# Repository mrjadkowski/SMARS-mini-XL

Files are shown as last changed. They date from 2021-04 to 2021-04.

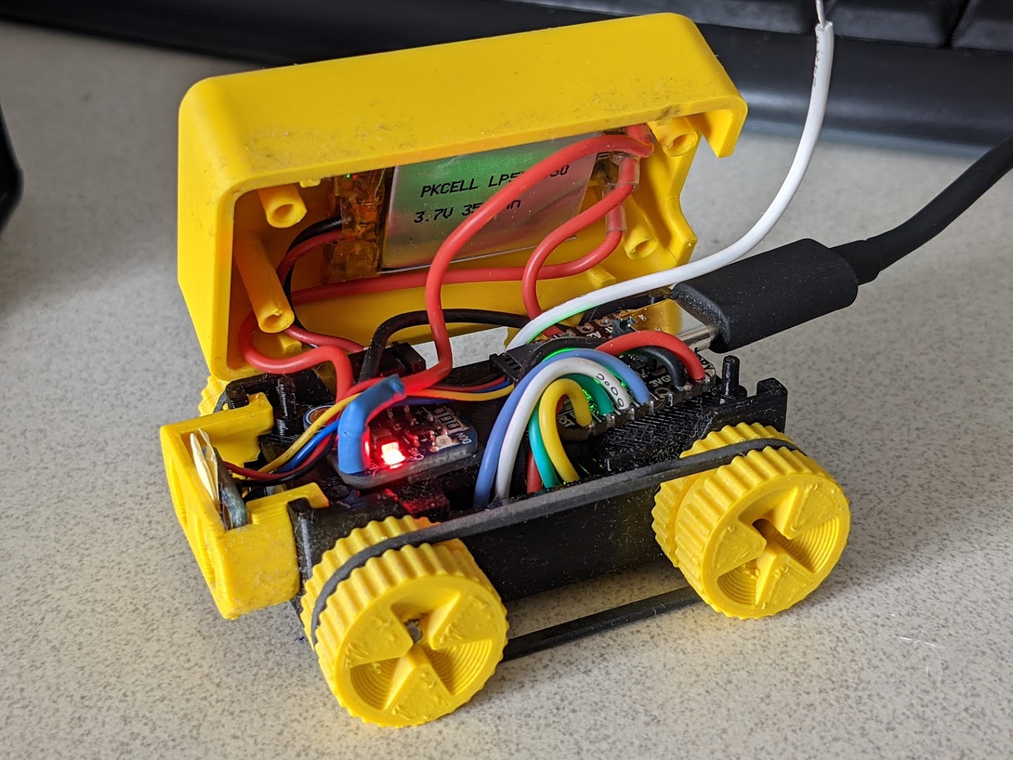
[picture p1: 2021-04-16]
Media/1.x.x/1.0.0 wiring.jpg

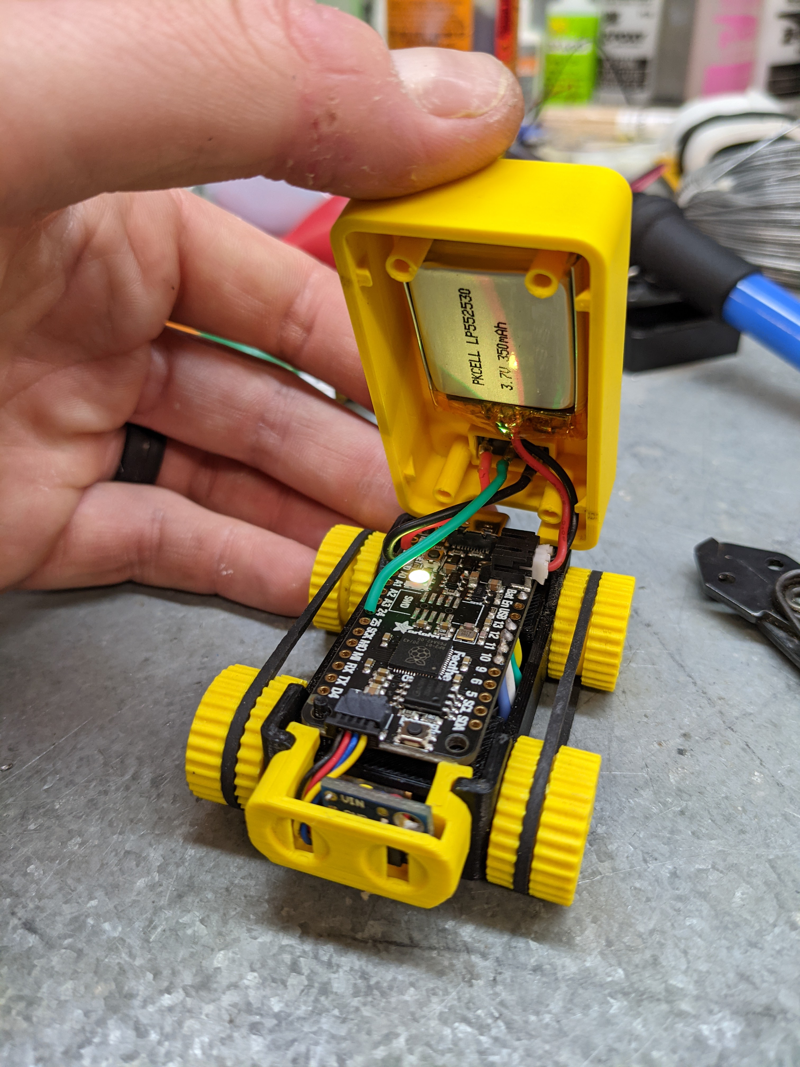
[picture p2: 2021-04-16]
Media/2.x.x/2.0.0 wiring.jpg

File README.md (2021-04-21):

# SMARS-mini-XL
### A small wheeled or tracked robot running on Circuit Python

Stemma QT board carrier face

#### I noticed that there has been a bump in traffic the last few days. I would love to have some collaborators on this project. I'm brand new to programming, brand new to CAD, brand new to GitHub, and brand new to 3D printing. About the only exiting skill I bring to this is soldering. Post an issue if you have a suggestion for a change, revise the 3D model, fork the code and improve it if you want, go crazy! I honestly have no idea what I'm doing and I know it can all be done better.

This repository has the 3D models, wiring details, and code for the SMARS mini XL. Currently the code is designed for Circuit Python 6.2.0 running on an Adafruit Feather RP2040. It uses a VL53L0X time-of-flight sensor and an APDS-9960 proximity/gesture/color/light sensor connected with i2c, an DRV8833 h-bridge motor driver, a small lipo, and a SPST switch. The code currently includes basic light seeking behavior while driving forward, obstacle detection and avoidance, and stuck detection that triggers an "unstuck" maneuver.

This project started as a remix of the "SMARS mini" design by [Kevin McAleer](https://www.youtube.com/user/kevinmcaleer28). I don't think it shares a single part with that design anymore, but it was an excellent starting point and gave the project an aesthetic theme that has certainly carried on. Thanks Kevin!

.STL and .STEP files are available in the CAD files folder (probably the most current) and at: https://www.thingiverse.com/thing:4810626

Current hardware BOM (this is the list of parts you need to buy and links to buy them): https://docs.google.com/spreadsheets/d/167UUY43PvzWUNg7vgtmYUr31faELwSrEWL3U5X_r1nM/edit?usp=sharing

The Media folder has a bunch of pictures and videos of various versions of the robot, including pictures of the wiring to see how things are routed.

Current code is running on the 2.x.x hardware setup. For the QT Py version, see the 1.1.0 release

See the Fritzing diagram for wiring.

See the code for the current required libraries; at the moment it requires:

  - adafruit_bus_device
  - adafruit_vl53l0x
  - adafruit_neopixel
  - adafruit_motor
  - adafruit_debouncer
  - adafruit_apds9960

The following parameters can be changed in the setup section of the code to alter the behavior:

  - start_turn_distance: the distance from an obstacle that the robot will stop and begin to pivot right
  - turn_time: the amount of time the robot will pivot to the right once started
  - stop_turn_distance: the distance from an obstacle that the robot will stop pivoting and start driving forward again, assuming turn_time has elapsed
  - abort_turn_time: if the robot has not reached stop_turn_distance in this amount of time while pivoting, it will attempt an unstuck maneuver
  - stuck_variance: if the robot moves less than this distance in 1 second, a stuck_counter event is recorded.

The NeoPixel on the RP2040 is used to show different states. The color codes are:
  - Green: driving forward
  - Red: obstacle detected and turning
  - Blue: stuck event detected, performing unstuck maneuver
  - Bright white: three consecutive unstuck maneuvers have failed

### Upcoming planned releases:
  - 3.0.0: Addition of solar charging, light-seeking behavior, and sleep logic to the 2.0.0 driving behavior. The end goal is to allow the robot to run perpetually, always trying to keep the battery charged as much as possible.

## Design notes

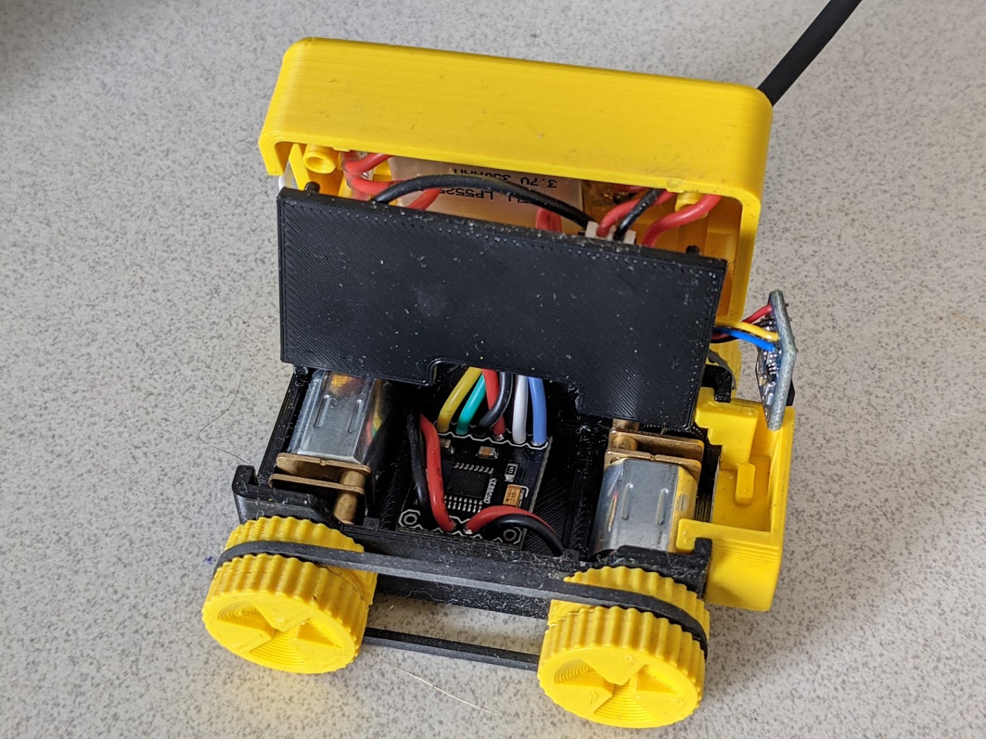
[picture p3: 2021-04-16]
Media/1.x.x/motors and driver.jpg

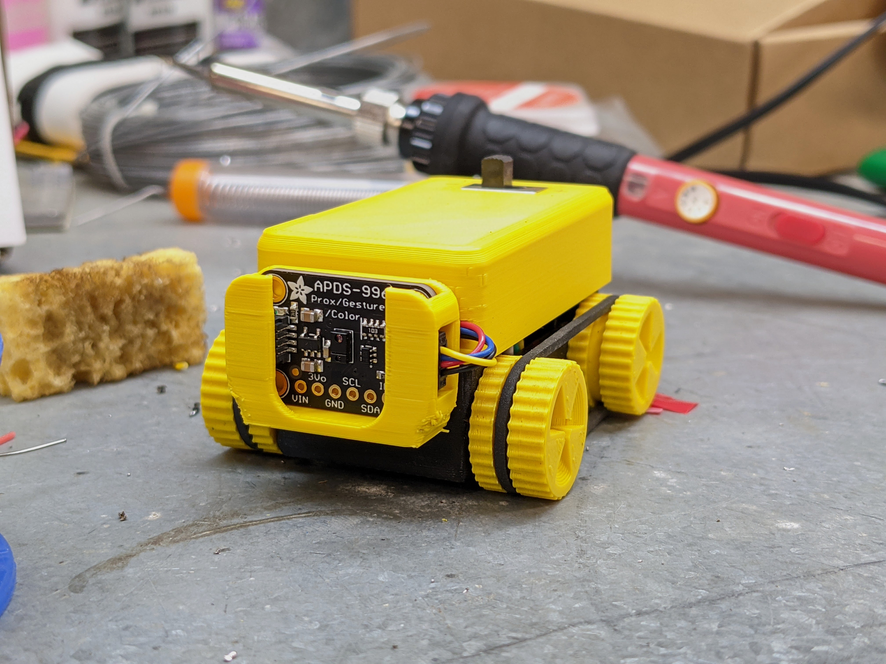
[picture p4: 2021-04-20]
Media/2.x.x/Stemma QT board carrier face.jpg

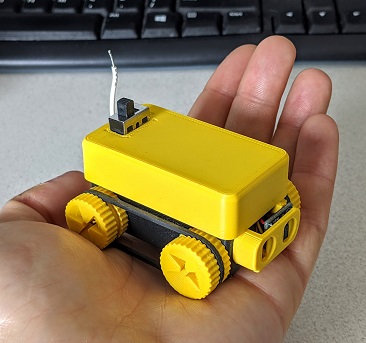
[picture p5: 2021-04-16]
Media/1.x.x/handheld.jpg

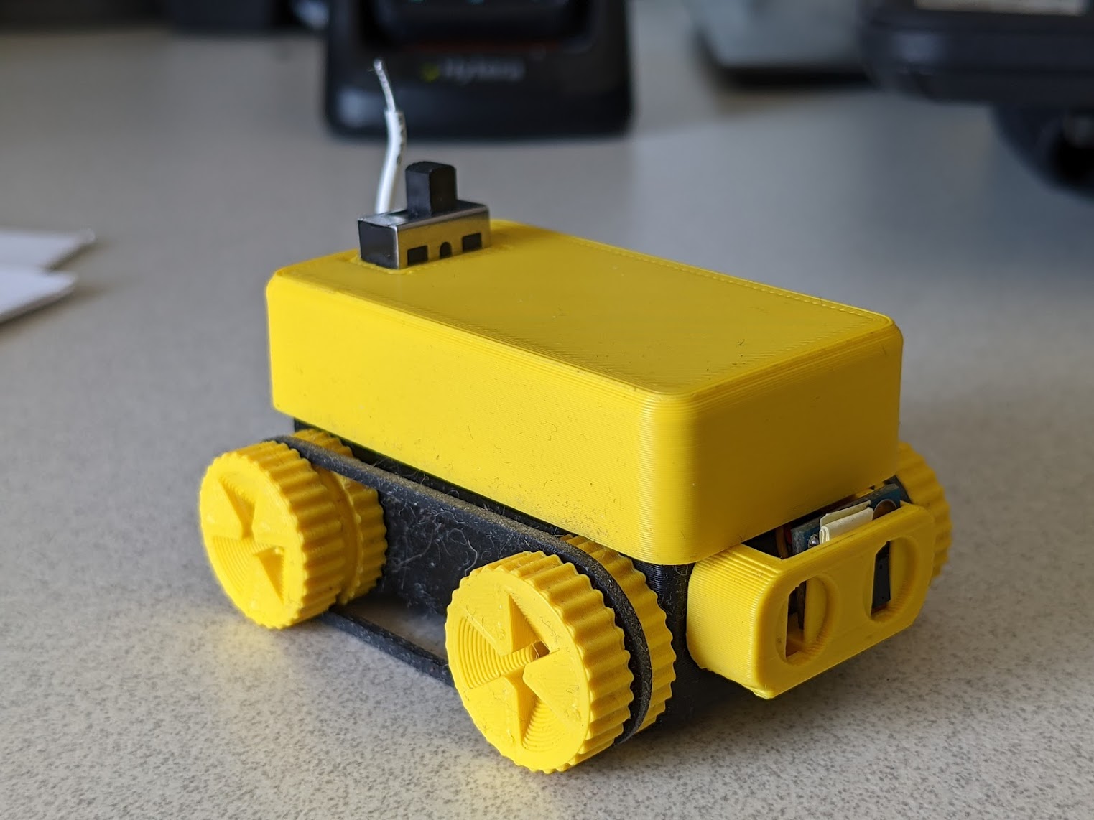
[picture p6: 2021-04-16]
Media/1.x.x/1.0.0.jpg

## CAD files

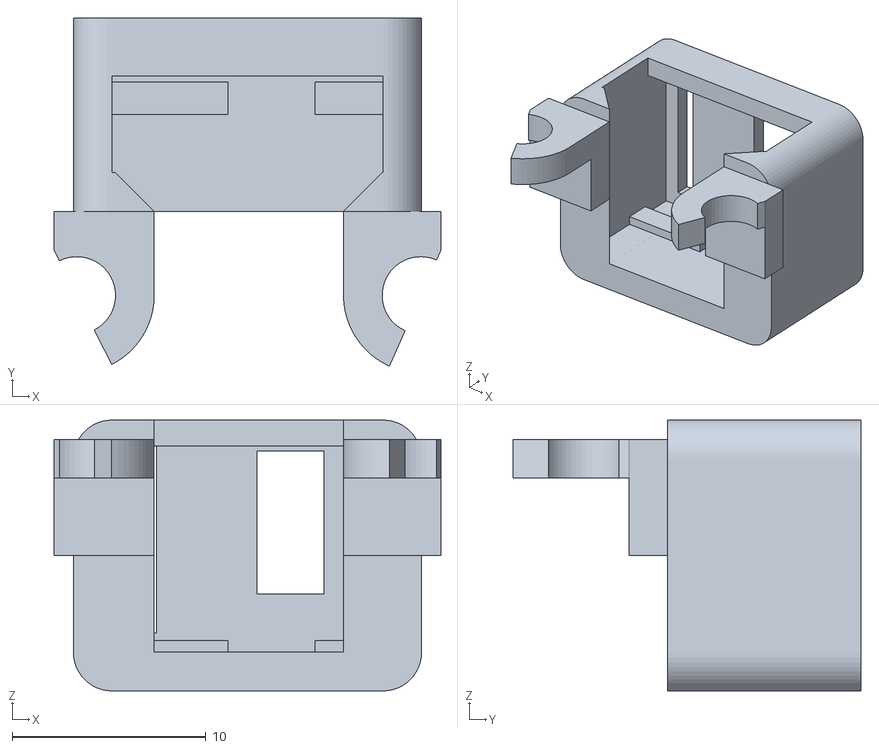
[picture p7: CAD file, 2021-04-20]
CAD files (STL and STEP)/GY-530 Rear Carrier.stl
20.0 x 18.0 x 14.0

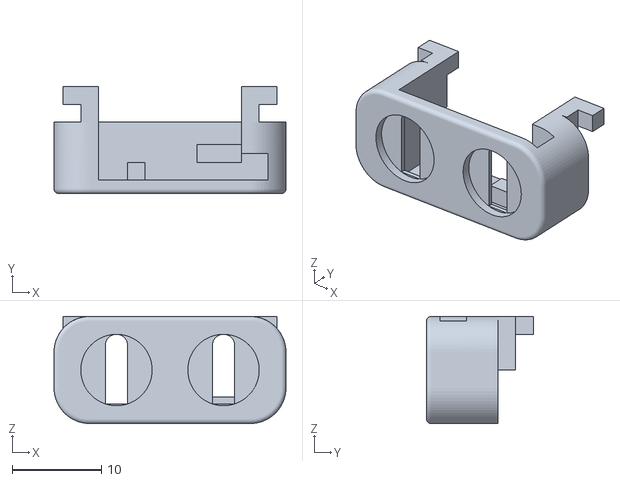
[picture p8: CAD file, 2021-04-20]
CAD files (STL and STEP)/GY-530 Face.stl
26.0 x 12.0 x 12.0

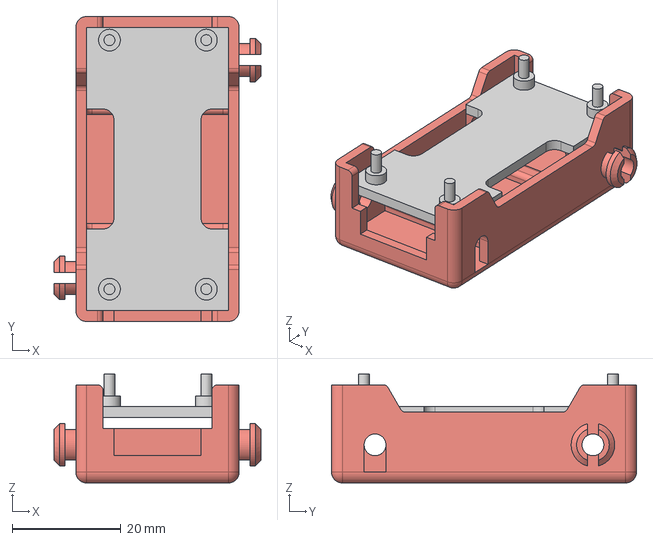
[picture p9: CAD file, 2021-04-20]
CAD files (STL and STEP)/SMARS mini XL 2-0-0.step
38.0 x 56.0 x 20.0 mm
Chassis
Feather support

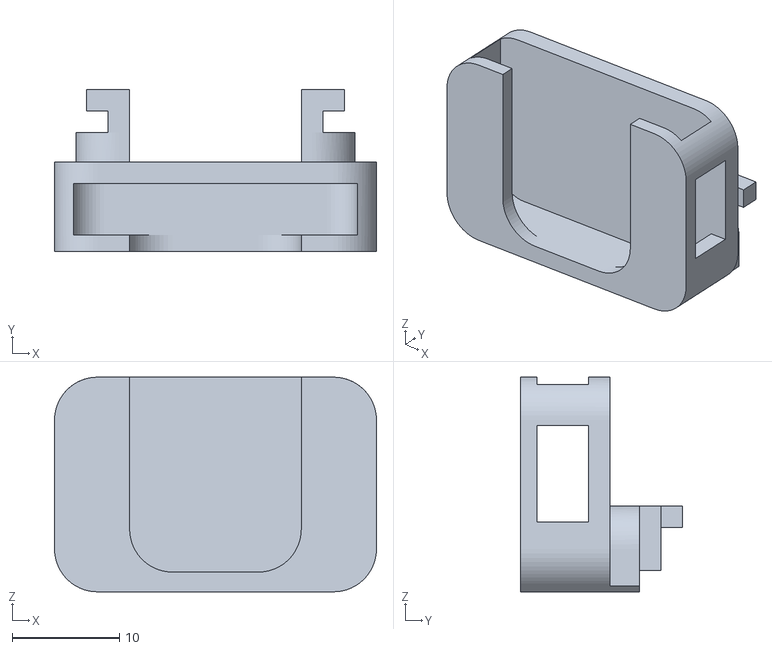
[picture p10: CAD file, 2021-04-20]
CAD files (STL and STEP)/APDS-9960 face.stl
30.0 x 15.0 x 20.0

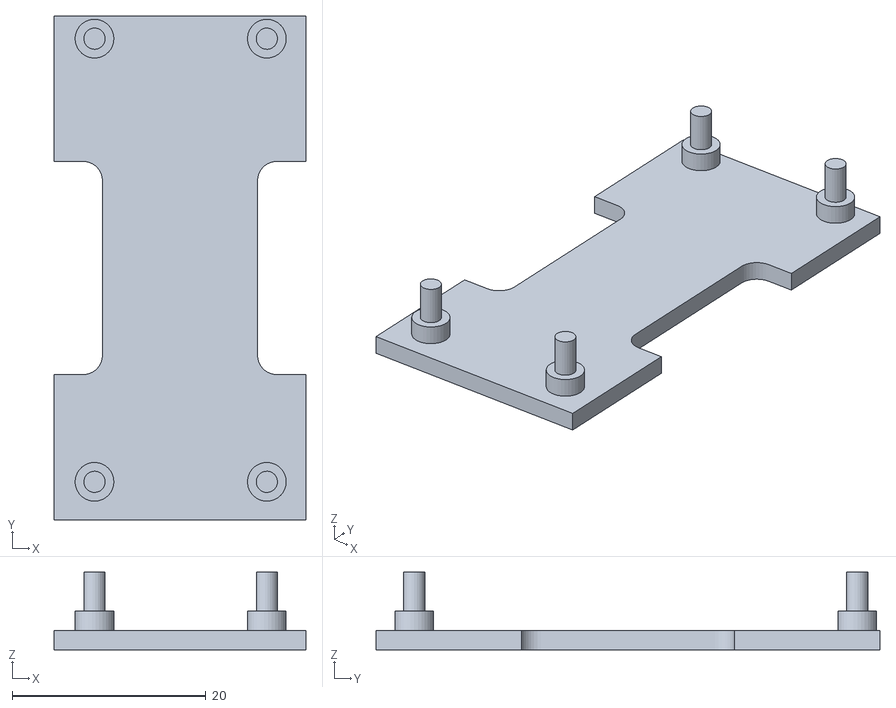
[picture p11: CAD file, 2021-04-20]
CAD files (STL and STEP)/Feather support.stl
26.0 x 52.0 x 8.00

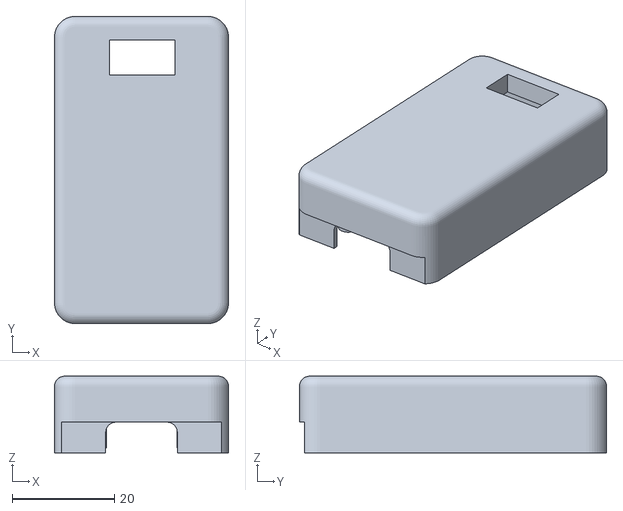
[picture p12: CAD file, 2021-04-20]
CAD files (STL and STEP)/Top Cover.stl
34.0 x 60.0 x 15.0

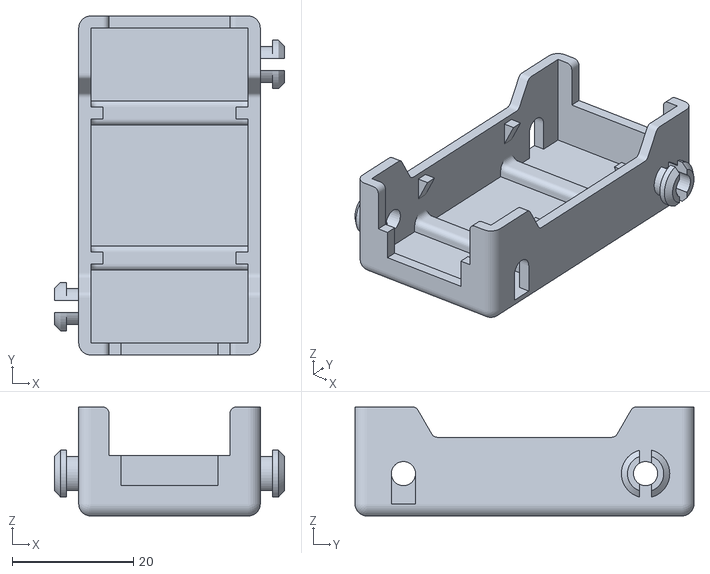
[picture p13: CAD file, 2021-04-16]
CAD files (STL and STEP)/Chassis.stl
38.0 x 56.0 x 18.0

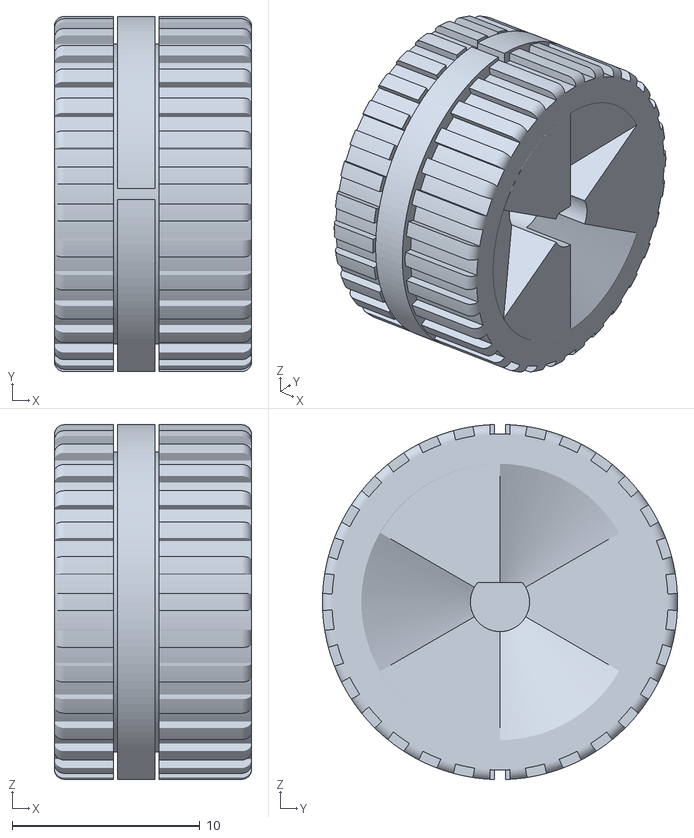
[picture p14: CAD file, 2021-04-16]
CAD files (STL and STEP)/Rubber band drive wheel.stl
10.5 x 18.9 x 18.9

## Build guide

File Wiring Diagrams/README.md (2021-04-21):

These wiring diagrams mostly reflect the actual wiring, with a few exceptions:
 - This design does not actually use the Adafruit DRV8833 motor controller breakout board. It is just the only Fritzing DRV8833 motor controller breakout board I could find. The BOM has a link to the actual board that is used. Becase of this, the actual wiring connections on the actual motor controller board are slightly different than the design. On the actual board, the inputs are labeled IN1 - IN4. The motor outputs are labeled OUT1 - OUT 4. To go between the diagram and the actual wiring: AIN1 = IN1, AIN2 = IN2, BIN1 = IN3, BIN2 = IN4. AOUT1 = OUT1, AOUT2 = OUT2, BOUT1 = OUT3, BOUT2 = OUT4.
 - The APDS-9960 connects using the Stemma QT connector, but the Fritzing object doesn't include that connector so it shows the hardwired connections. Use a pre-made Stemma QT cable from Adafruit to connect from the Stemma QT connector on the APDS-9960 (or any other Stemnma QT sensor board) to the Stemma QT connector on the RP2040. Cut a second Stemma QT cable in half and extend the wires to reach the GY-530 on the rear of the robot.

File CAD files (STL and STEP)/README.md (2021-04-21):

## Printing notes for printing these parts successfully
### Materials and print settings.
I printed in a mix of ASA (yellow) and PETG (black), but only so I could have different colors. I don't think the materials choice really matters as long as your printer settings are good. There are a lot of small round towers involved so layer adhesion is important. I printed everything with a .2mm layer height and 10% infil. 
### Notes for individual parts
#### Rubber Band Drive Wheel
You need four of these. The .STL file includes supports already. Print them flat face down. Once the part has totally cooled you can remove the center support by using a thumb tack or other small metal tool to lever the cylinder to the side. It should snap away cleanly from the inside of the wheel hub. Remove each half of the groove support by sliding the same thumb tack in between the two halves and then under one. Lever it up, and then you should be able to grab it with your fingers and pull it away. Repeat for the other side.

Depending on the mix of materials you use, and how much they contract when cooling, you may have to adjust the scale of these by 1-2% either way for the right fit. These fit perfectly at 100% scale for me using ASA. When they snap on to the wheel hubs on the chassis, they will initially be a snug fit, but they break in to spin freely and have very little play.
#### APDS-9960 Face
Print this right-side-up (same orientation as when it is installed on the robot). It will require some supports under the overhangs on the rear that attach it to the chassis.
#### Chassis
Print this right-side-up (same orientation as when it is installed on the robot). It will require supports under the overhanging wheel hubs for the non-driven wheels.
#### GY-530 Rear Carrier
Print this face-down (tabs up). It doesn't require supports.
#### Feather Support
Print this right-side up (posts up). It doesn't require supports.
#### Top Cover
Print this upside-down (flat-surface down). It doesn't require supports.

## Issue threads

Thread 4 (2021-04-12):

Stuck detection generates erroneous stuck events

mrjadkowski, 2021-04-12:
Proximity sensor is reading roughly the same distance ahead of the robot while driving on flat ground (particularly on carpet) and the constant distance reading is triggering the stuck detection logic when the robot is not stuck

mrjadkowski, 2021-04-12:
Move ToF/prox sensor higher?

mrjadkowski, 2021-04-20:
Tried angling the sensor up slightly and it is a little better but erroneous stuck events are still happening when the robot is in wide open spaces. I think it might be cause by the sensor reading max range (8190), even though the code should reject any readings above 8000.

mrjadkowski, 2021-04-20:
This may have been fixed in the 2.1.0 code by lowering stuck_variance to 10 from 20. It seems to be working now but I'm going to do more testing before closing the issue.

mrjadkowski, 2021-04-21:
Still not perfect.  It occasionally has an erroneous stuck event when in an open area, or doesn't detect that it is stuck. It's probably 90% reliable, but needs to be better. Some ideas:

Tune the "stuck_variance" parameter to minimize erroneous events
Maybe move the LOS of the sensor even higher? It's gonna block the USB connector though.
Use a longer-range ToF sensor that can detect further distances to minimize non-detect events

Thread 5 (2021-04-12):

Stuck detection fails when robot is pitched up

mrjadkowski, 2021-04-12:
If the robot gets stuck trying to drive up and over an obstacle (like trying to get on to carpet) the range sensor doesn't produce a reading if there isn't a close obstacle, and the stuck detection logic is not triggered.

mrjadkowski, 2021-04-20:
Moved ToF sensor to the rear

Closed 2021-04-20.

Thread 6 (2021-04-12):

Obstacle detection triggers when pitched down

mrjadkowski, 2021-04-12:
When going over a ledge the range sensor on the front will go below start_turn_distance and trigger a turn.

mrjadkowski, 2021-04-12:
Move ToF/Prox sensor LOS higher?

mrjadkowski, 2021-04-20:
Moved ToF sensor to the rear in latest design

Closed 2021-04-20.

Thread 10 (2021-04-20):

APDS-9960 can't do gesture detection and proximity simultaneously

mrjadkowski, 2021-04-20:
Probably best to switch to the VCNL-4040 sensor since it's cheaper and still supports both light and proximity. The APDS-9960 works fine but gestures must be enabled and then the gesture proximity threshold set to 255 to inhibit any gesture detection.

mrjadkowski, 2021-04-20:
Turns out you can just turn off gesture detection and it has the same effect.

mrjadkowski, 2021-05-08:
Made some small changes to use VCNL-4040 and it works great. Solar charging branch is now using VCNL-4040 instead of the APDS sensor

Closed 2021-05-08.

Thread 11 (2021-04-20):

Rubber bands come off the wheels

mrjadkowski, 2021-04-20:
If they aren't tight to begin with, or if they stretch out over time, they come out of the grooves during pivot turns and then jam up the wheels.

mrjadkowski, 2021-04-21:
#56 o-rings (1-1/2 in. OD x 1-3/8 in. ID x 1/16 in. wall, or metric equivalent) work much better than #16 rubber bands. BOM updated to spec those o-rings instead of rubber bands.

Closed 2021-04-21.

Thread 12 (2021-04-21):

Required parts list

thisiscetin, 2021-04-21:
Can you add the required electronic and mechanical parts used in this robot as a list to README?
I have checked the design and it looks like everything is there. I just want to order parts same brand as yours, assemble them without a problem. It may also be good to put 3D printing details like infill, support needed, layer height etc. share the experience on parts them also.

mrjadkowski, 2021-04-21:
The parts listing is in the BOM (Bill of Materials) that is linked in the README. It's a Google Sheets document. Order the 2.x.x parts. If you want to try solar charging get the "future solar charging hardware" as well. That's what I just ordered to try solar charging with mine.

Most of those 3D printing details are on the Thingiverse page, but I like the idea of adding a README to the CAD filed folder here so it is all in one place. The CAD filed folder has the most current design stuff anyways. I'll do that later today.

mrjadkowski, 2021-04-21:
I added a README to the CAD files folder that has all the details for printing.

Closed 2021-04-21.

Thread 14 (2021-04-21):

Slide switch wiring is awful

mrjadkowski, 2021-04-21:
Changes to make:
 - use digitalio.pull to pull pin down so only two wires are needed
 - change to micro pushbutton switch
 - put switch on chassis instead of the top cover so only the battery wire connects the top cover to the board
 - use slide switch for battery disconnect instead

mrjadkowski, 2021-05-08:
All these changes are incorporated in the solar charging branch

Closed 2021-05-08.

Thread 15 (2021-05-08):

AttributeError: object 'module' does not have attribute 'VL53L0X'

Fredic91, 2021-05-08:
Hello
I'm trying to make the mini robot Smars. I printed and assembled everything and started testing the software. (Github files)
I'm a newbie to CircuitPython, usually I code in C / C ++.
I have a problem with this library:
Traceback (most recent calls last):
File "code.py", line 39, in
AttributeError: object 'module' does not have attribute 'VL53L0X'

What do you think?
Thanks

I m using :
Windows 10
Mu 1.0.2 and Mu 1.1.0.beta.4
adafruit-circuitpython-bundle-6.x-mpy-20210506
Adafruit CircuitPython 6.2.0 on 2021-04-05;
Adafruit Feather RP2040 with rp2040

mrjadkowski, 2021-05-08:
Based off your pictures I think you should be using the 2.0.0 code. If that is the case, most likely you don't have the VL530L0X module in the lib folder on your CircuitPy drive

mrjadkowski, 2021-05-08:
Check the readme in the 2.0.0 release for all the required libraries

Fredic91, 2021-05-08:
lib/directory VL53L0X only contain a file requirements.txt :
# SPDX-FileCopyrightText: 2021 ladyada for Adafruit Industries
#
# SPDX-License-Identifier: Unlicense
Same for adafruit_neopixel
Thanks

>
>
> Check the readme in the 2.0.0 release for all the required libraries

lib/directory VL53L0X only contain a file requirements.txt :
# SPDX-FileCopyrightText: 2021 ladyada for Adafruit Industries
#
# SPDX-License-Identifier: Unlicense
Same for adafruit_neopixel
Thanks

Fredic91, 2021-05-08:
sorry I closed the issue by mistake

    Le samedi 8 mai 2021 à 18:57:18 UTC+2, mrjadkowski ***@***.***> a écrit :

Based off your pictures I think you should be using the 2.0.0 code. If that is the case, most likely you don't have the VL530L0X module in the lib folder on your CircuitPy drive

—
You are receiving this because you authored the thread.
Reply to this email directly, view it on GitHub, or unsubscribe.

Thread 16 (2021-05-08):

import module problems

Fredic91, 2021-05-08:
lib/directory VL53L0X only contain a file requirements.txt
Same for adafruit_neopixel
Thanks

mrjadkowski, 2021-05-08:
Ah, you need to have the .mpy library files, not necessarily the directories.

https://learn.adafruit.com/welcome-to-circuitpython/circuitpython-libraries

Fredic91, 2021-05-09:
thank you very much, I will study this more closely!

    Le samedi 8 mai 2021 à 20:18:38 UTC+2, mrjadkowski ***@***.***> a écrit :

Ah, you need to have the .mpy library files, not necessarily the directories.

https://learn.adafruit.com/welcome-to-circuitpython/circuitpython-libraries

—
You are receiving this because you authored the thread.
Reply to this email directly, view it on GitHub, or unsubscribe.

Fredic91, 2021-05-09:
on any photo can we see the 2 sensors installed? vl53l0x and apds9960 ... how do you do?

    Le samedi 8 mai 2021 à 20:18:38 UTC+2, mrjadkowski ***@***.***> a écrit :

Ah, you need to have the .mpy library files, not necessarily the directories.

https://learn.adafruit.com/welcome-to-circuitpython/circuitpython-libraries

—
You are receiving this because you authored the thread.
Reply to this email directly, view it on GitHub, or unsubscribe.

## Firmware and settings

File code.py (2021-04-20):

# this is designed to run on an adafruit Feather RP2040 board running Circuit Python 6.2.0
# using a VL53L0X ToF sensor, APDS-9960 proximity sensor, and a DRV8833 motor driver.

import board
import time
import busio
import adafruit_vl53l0x
import pwmio
import neopixel
from digitalio import DigitalInOut, Direction
from adafruit_debouncer import Debouncer
from adafruit_motor import motor
from adafruit_apds9960.apds9960 import APDS9960
from adafruit_apds9960 import colorutility

# set up PWM pins for left motor
PWM_PIN_A = board.D12  # yellow wire
PWM_PIN_B = board.D11  # green wire

# set up PWM pins for right motor
PWM_PIN_C = board.D10  # white wire
PWM_PIN_D = board.D9  # blue wire

# set up left motor
pwm_a = pwmio.PWMOut(PWM_PIN_A, frequency=50)
pwm_b = pwmio.PWMOut(PWM_PIN_B, frequency=50)
leftmotor = motor.DCMotor(pwm_a, pwm_b)

# set up right motor
pwm_c = pwmio.PWMOut(PWM_PIN_C, frequency=50)
pwm_d = pwmio.PWMOut(PWM_PIN_D, frequency=50)
rightmotor = motor.DCMotor(pwm_c, pwm_d)

# initialize i2c and time of flight sensor
i2c = busio.I2C(board.SCL, board.SDA)
tof = adafruit_vl53l0x.VL53L0X(i2c)

# initialize APDS-9960
apds = APDS9960(i2c)
apds.enable_proximity = True
apds.enable_color = True

# initialize NeoPixel
neopixel = neopixel.NeoPixel(board.NEOPIXEL, 1)

# setup switch input
switch = DigitalInOut(board.D24)
switch.direction = Direction.INPUT
switch_debounced = Debouncer(switch)

# set up turn and drive parameters
start_turn_distance = 5
stop_turn_distance = 2
turn_time = 1.5
abort_turn_time = 5
start_turn_time = -1
turn_flag = False
run_flag = False
turn_right_flag = True

# set up stuck decetion
stuck_check_last = 0
stuck_timer = 0
stuck_counter = 0
stuck_sequential_counter = 0
stuck_range = tof.range
stuck_variance = 10
stuck_flag = False

# set up light detection
last_lux = 0

while True:
    now = time.monotonic()

    # update light data, calcuate lux
    r, g, b, c = apds.color_data
    lux = colorutility.calculate_lux(r, g, b)

    # set run_flag to true if switch was switched on
    switch_debounced.update()
    if switch_debounced.rose:
        run_flag = True
    # set run_flag to false of switch was switched off
    if switch_debounced.fell:
        run_flag = False
        neopixel.fill((0, 0, 0))

    # when start_turn_distance or less from an obstacle, set turn flag
    if apds.proximity >= start_turn_distance:
        turn_flag = True

    # if c > 600:
        # run_flag = False

    # if run_flag is true, then drive
    if run_flag:
        # if stuck for more than 20 seconds, stop driving
        if stuck_sequential_counter >= 3:
            run_flag = False
            neopixel.fill((255, 255, 255))

        elif stuck_flag:
            neopixel.fill((0, 0, 10))
            # back up for one seconds
            if now <= stuck_timer + 1.0:
                leftmotor.throttle = -0.5
                rightmotor.throttle = -0.5

            # turn left for two seconds
            elif now <= stuck_timer + 3.0:
                leftmotor.throttle = -0.5
                rightmotor.throttle = 0.5

            # go back to driving
            else:
                stuck_flag = False
                turn_flag = False
                start_turn_time = now
                stuck_counter = 0
                stuck_sequential_counter += 1

        elif turn_flag:
            neopixel.fill((10, 0, 0))

            # set stuck_flag if attempting to turn for more than abort_turn_time
            if now > abort_turn_time + start_turn_time:
                stuck_flag = True
                stuck_timer = now
                turn_flag = False

            # turn right for turn_time or until stop_turn_distance or more from an obstacle
            elif apds.proximity > stop_turn_distance or now <= start_turn_time + turn_time:
                leftmotor.throttle = 0.5
                rightmotor.throttle = -0.5

            else:
                turn_flag = False
                print(turn_right_flag)
                turn_right_flag = not turn_right_flag
                last_c = 0
                start_turn_time = now

        # drive straight forward seeking light when greater than start_turn_distance from an obstacle
        else:
            neopixel.fill((0, 10, 0))
            if lux < last_lux:
                turn_right_flag = not turn_right_flag

            if turn_right_flag:
                leftmotor.throttle = 0.7
                rightmotor.throttle = 0.3

            if not turn_right_flag:
                leftmotor.throttle = 0.3
                rightmotor.throttle = 0.7

            # forward stuck logic
            # perform stuck check once every second
            if now >= stuck_check_last + 1:
                stuck_check_last = now

                # reset stuck_counter and stuck_sequential_counter if not stuck
                if tof.range > stuck_range + stuck_variance or tof.range >= 8000:
                    stuck_counter = 0
                    stuck_sequential_counter = 0

                # increment stuck_counter if stuck
                if tof.range <= stuck_range + stuck_variance and tof.range < 8000:
                    stuck_counter += 1

                # reset stuck_range for next check
                stuck_range = tof.range

                # set stuck_flag to True if stuck for seven consecutive seconds, increment stuck_sequential_counter
                if stuck_counter >= 7:
                    stuck_flag = True
                    stuck_timer = now

            start_turn_time = now
            # if c != last_c: print(c)
            last_lux = lux

    # if run_flag is false, shut off motors and reset flags
    else:
        leftmotor.throttle = 0
        rightmotor.throttle = 0
        turn_flag = False
        stuck_flag = False
        turn_right_flag = True
        stuck_counter = 0
        stuck_sequential_counter = 0

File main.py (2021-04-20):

import board
import busio
import time
from adafruit_apds9960.apds9960 import APDS9960
from adafruit_apds9960 import colorutility

i2c = busio.I2C(board.SCL, board.SDA)

apds = APDS9960(i2c)
apds.enable_proximity = True
apds.enable_gesture = True
apds.enable_color = True

apds.gesture_proximity_threshold = 255

# Uncomment and set the rotation if depending on how your sensor is mounted.
# apds.rotation = 270 # 270 for CLUE

while True:
    print(apds.proximity)
    print(apds.color_data)
    r, g, b, c = apds.color_data
    lux = colorutility.calculate_lux(r, g, b)
    print(lux)
    time.sleep(1)

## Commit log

2021-04-06 Create Wiring sketch.fzz
    [Wiring sketch.fzz]
2021-04-06 Added motor initialization
    [Wiring sketch.fzz]
2021-04-06 added details for charging circuit
2021-04-06 added tof printout for troubleshooting
2021-04-06 added 30mm hysteresis for obstacle avoidance
    [code.py]
2021-04-07 Update Wiring sketch.fzz
    [Wiring sketch.fzz]
2021-04-08 Added touch on/off
    uses capacitive touch input on D6 to start/stop drive program
2021-04-09 Removed breadboard wiring
    [Wiring sketch.fzz]
2021-04-09 Added basic stuck detection
    [code.py]
2021-04-10 Improved stuck detection logic
    isolated stuck detection logic code into driving straight mode
    Eliminited ToF sensor max range (8190) from logic
    Stuck counter now resets if there is a non-stuck iteration
    [code.py]
2021-04-10 Changed stuck detection logic to use time.monotonic
    [code.py]
2021-04-11 tuned stuck detection code
    [code.py]
2021-04-11 Added solar charging logic.drawio
2021-04-11 Update solar charging logic.drawio
2021-04-12 Code clean up
    Removed commented debugging print commands and changed a couple of comments to reflect actual code
2021-04-12 Fixed stuck behavior bug
    If turn_flag was triggered during unstuck maneuver, robot would get stuck in perpetual loop turning back to the place it was stuck
    [code.py]
2021-04-14 Wiring changes
    Renamed 1.x.x wiing sketch to reflect code version, and started working on 2.x.x wiring sketch
    [1-x-x wiring.fzz, 2-x-x wiring.fzz]
2021-04-14 Added CAD files
    STLs for printing and STEP for design modification
    [Chassis V7.stl, Face V7.stl, Feather support V7.stl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]
2021-04-14 Changed run switch to pull D25 up when enabled
    [2-x-x wiring.fzz]
2021-04-15 Ported to run on RP2040 board
    Wired IAW 2.x.x wiring diagram
    [2-x-x wiring.fzz]
2021-04-15 Added neopixel and debounced switch
2021-04-15 Fixed stuck logic bug
    set switch to detect rose and fell events instead of total state. Also tweaked neopixel behavior (shuts off when switch is off, goes full bright when stops driving because stuck
    [code.py]
2021-04-16 Update 2-x-x wiring.fzz
    [2-x-x wiring.fzz]
2021-04-16 Added design for APDS-9960 face
    [APDS-9960 face v13.stl, GY-530 Face V7.stl, SMARS mini XL v13.step]
2021-04-16 Minor tweaks to feather supports and faces
    [APDS-9960 face v13.stl, APDS-9960 face.stl, Chassis V7.stl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]
2021-04-16 Update APDS-9960 face.stl
    adjusted tolerances for board fit
    [APDS-9960 face.stl]
2021-04-18 APDS-9960 addition
    Changed obstacle detection code to use APDS-9960 proximity data.
    Changed stuck detection code to use ToF sensor located on back of chassis.
    Added STL files for rear GY-530 carrier and front Stemma QT board carrier (for APDS-9960)
    [APDS-9960 face.stl, Feather support.stl, GY-530 Rear Carrier.stl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]
2021-04-20 Added pictures of stemma QT board carrier and rear sensor carrier
2021-04-20 Fixed 2.x.x wiring diagram
    Old one got wiped out somehow
    [2-x-x wiring.fzz]
2021-04-20 Renamed .STEP files to reflect hardware/software versions
    [SMARS mini XL 2-0-0.step]
2021-04-20 Turned off gesture detection
    It was an unnecessary workaround
    [code.py]
2021-04-21 Added wiring notes
2021-04-21 wiring notes
2021-04-21 Added STEMMA QT wiring details
